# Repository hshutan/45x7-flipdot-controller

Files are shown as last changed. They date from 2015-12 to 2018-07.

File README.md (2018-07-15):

**This project is old! I do not recommend my hardware based project anymore, check out my RS-485 protocol-based projects! [Main Flipdot Project Page Here](https://github.com/hshutan/FlipDotCompendium)**

---

Flip Dot Animation 1

# 45x7-flipdot-controller
Custom PCB controller board for a single 45x7 flip dot panel from a Luminator MAX3000 SideSign

PCBFront PCBBack

Finished PCB Flip Dot Animation 2 

# How To

**A much more [detailed How To](#detailed) is below**

You will need the following items to assemble a flip dot sign using my PCB

1. The PCB in this github project which can be ordered from [OSH Park](https://oshpark.com/shared_projects/JROcn5LK) or another fab.
2. [My simple Arduino clock program](https://github.com/hshutan/FlipDotDisplay_Clock1_SWv1) which contains my `Matrix_CoProcessor` library, a library specifically built to drive this PCB.
3. Surface mount silicon parts: see the [Digi-Key BOM file](https://github.com/hshutan/45x7-flipdot-controller/blob/master/FlipDotBOM.csv)
  - Note that the Digi-Key BOM does not include the two through hole capacitors you will need.
4. A Luminator MAX3000 Side Sign.
  - I purchased mine from [Rollsign Gallery](http://rollsigngallery.com/). A single Luminator MAX3000 side sign will have two 45x7 display panels inside, which are very easy to remove.
5. A microcontroller or Arduino, and various power supply components to provide the different needed voltages.
  - I like Paul Stoffregen's Arduino compatible [Teensy](http://www.pjrc.com/) but often use [Arduino Pro Mini](https://www.arduino.cc/en/Main/ArduinoBoardProMini) clones from eBay for less demanding projects.

# Notes
The silkscreen for the 64 pin connector is for aesthetics. You should install the connector on the back of the board not the front, using the silkscreen for orientation reference only.

There are three voltages: Logic (5v), Flip (12-15v), LED (19v or 400mA max)

HW Rev1 of the PCB does not include any current limiting for the flip dots, or for the LEDs. I am using a 60mA current limiter in-line with the flip dot voltage line. The dots seem to flip best based on voltage and not current, which is why I am using such a small current. The LEDs are meant to be driven at 19 volts max, however less is safer. A current limit of 350mA would be safe for the LEDs.

My first prototype clock/sign with this PCB uses 15 volts for both the LEDs and flip dots. This means the LEDs are always on, although not near their maximum brightness. I am using a 5 volt Arduino Pro Mini, and also supplying 5 volts to the logic voltage input on the PCB.

Watch for ground loops, as I believe these cause weak/un-reliable flips. Because the grounds are all "commoned" on the PCB, do not tie any of your grounds together pre-PCB.

Luminator and MAX3000 are trade names of the Luminator Technology Group, not mine.

# Detailed How To / Step by Step Instructions
1. Acquire a Luminator MAX3000 Side Sign. I found mine on [Rollsign Gallery](http://rollsigngallery.com/).
  - A single Luminator side sign will contain two 45x7 panels.
2. Order the PCB in this github project, it can be ordered with a few clicks from [OSH Park](https://oshpark.com/shared_projects/JROcn5LK)
3. Order the bill of materials ([see CSV file](https://github.com/hshutan/45x7-flipdot-controller/blob/master/FlipDotBOM.csv))
  - Also grab two spare through hole capacitors from your parts bin. Try a 50 volt 330 microfarad for the flip voltage, and a 16 volt 100 microfarad capacitor for the logic voltage.
4. Take apart the MAX3000 side sign and remove both of the 45x7 panels.
5. Assemble the PCB by placing all components and soldering. Hot air can be used for all the surface mount components.
  - For aesthetics, the PCB has very little silk screen. Here is how to place components: Pin 1 of each IC is in the lower left of the land pattern when viewing the board from the top (see PCB pictures at the top of this page).
  - The 0805 (2012 Metric) pads in the lower right area of the PCB are for the pull-up and pull-down resistors.
  - The 0805 (2012 Metric) pads in the upper left of the PCB are for the 0.1 microfarad shift register supporting capacitors.
6. Program an Arduino or microcontroller with the [test pattern](https://github.com/hshutan/FlipDotDisplay_TestPatterns_SWv1) software. A good test pattern to start with is `testPattern2()`
7. Hook up the Arduino per the comments in the code:
  - Arduino Uno pin 11, to SER on PCB
  - Arduino Uno pin 13, to SCK on PCB
  - Arduino Uno pin 10, to RCK on PCB
  - Arduino 5v, to 5v+ on PCB
8. Connect a power supply (start with 10-12 volts) to GND and Flip+ on the PCB.
  - For prototyping, use a constant voltage/constant current power supply. This will allow you to limit the current to 100mA (or less) for safety, and also to test flip reliability at different voltages. If you are using my `Matrix_CoProcessor` library that comes with the [test pattern](https://github.com/hshutan/FlipDotDisplay_TestPatterns_SWv1) software, then there is little risk of a flip dot being energized for more than a few hundred microseconds, however you should still use current limiting of 100mA or less to prevent damage if any paths remain energized for too long.

# Thanks
I would like to thank the following sources:
- [Dottie the Flip Dot Clock](http://dhenshaw.com/Art/Dottie/start.html)
- [Rollsign Gallery](http://rollsigngallery.com/)

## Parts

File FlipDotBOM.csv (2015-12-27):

暼繢igi-Key Part Number | Manufacturer | Manufacturer Part Number | Customer Reference | Quantity 1 | Quantity 2 | Quantity 3 | Mfg Std Lead Time | Description | Comments | RoHS Status | Lead Free Status | REACH Status
5650458-5-ND | TE CONNECTIVITY AMP | 5650458-5 | AMPFEMALESOCK64OF96POS | 1 | 0 | 0 | 5 Weeks | CONN RECEPT 64 POS VERT DIN PCB |  | RoHS Compliant | Lead free | Not Available
490-1673-1-ND | MURATA ELECTRONICS (VA) | GRM21BR71E104KA01L | CAPFORSHIFTREGS | 13 | 0 | 0 | 18 Weeks | CAP CER 0.1UF 25V X7R 0805 | Alternate Packaging Exists | RoHS Compliant | Lead free | Unaffected Jun-2015
IRF7309PBFCT-ND | INFINEON TECHNOLOGIES AMERICAS CORP. (VA) | IRF7309TRPBF | NONCOMMONDRAINOEMPNFET | 52 | 0 | 0 | 12 Weeks | MOSFET N/P-CH 30V 4A/3A 8SOIC | Alternate Packaging Exists | RoHS Compliant | Lead free | Unaffected Jun-2015
296-26485-1-ND | TEXAS INSTRUMENTS (VA) | SN74HC595NSR | TILATCHINGSHIFTREGR | 13 | 0 | 0 | 6 Weeks | IC SHIFT REGISTER 8BIT 16SO | Alternate Packaging Exists | RoHS Compliant | Lead free | Unaffected Dec-2014
NSI45060JDT4GOSCT-ND | ON SEMICONDUCTOR (VA) | NSI45060JDT4G | CURLIMTR | 1 | 0 | 0 | 13 Weeks | IC LED DRVR SBT CCR DPAK | Alternate Packaging Exists | RoHS Compliant | Lead free | Unaffected Jun-2015
YAG1319CT-ND | YAGEO (VA) | RC0805FR-0710KP | 10K1%2012 | 14 | 0 | 0 | 22 Weeks | RES SMD 10K OHM 1% 1/8W 0805 | Alternate Packaging Exists | RoHS Compliant | Lead free | Unaffected Jun-2015

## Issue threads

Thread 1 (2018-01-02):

Problem switching off high side P channel MOSFETs

iiliev, 2018-01-02:
Thank you so much for posting your project! I did get one of these MAX3000 flip dot displays with no driver and your schematic is the closest to what I need (mine is 16x28 though). The principle of operation is clear, the code works fine, I can't figure out how are you switching off the high side P channel MOSFETs though. The P channel MOSFET in IRF7309TRPBF has a switching voltage of -1V. When you power the load (the flip dot display in this case) with say 12V and the switching voltage (from Arduino/microcontroller/SN74HC595/etc) is 5V the gate sees -7V. On the Eagle schematic you posted it seems that all MOSFETs are driven directly by the SN74HC595. Am I missing something (the only way I know how to do this would be with at least one extra transistor)? Appreciate your help...

hshutan, 2018-01-03:
Hi! Happy to share the project. Hopefully I can help. I will say that it is _very_ possible that I am not using components (like PNP/NPN transistors) _entirely_ correctly...but the clock I built is still running 24/7 perfectly!

The way I am using these MOSFETs from my hobby-level understanding, is that a logic HIGH (5v) from a shift register going to an NPN's gate or base would turn that NPN 'switch' on. A logic HIGH (5v) from a shift register going to a PNP's gate or base would turn that PNP 'switch' off. Same thing in reverse, logic LOW (0v) would turn an NPN off and a PNP on. That's why the idle or steady state of the shift registers is a stream of alternating 1's and 0's, it sets all the PNPs turned off with logic HIGHs, and all the NPNs turned off with logic LOWs.

I don't think I understand what you mean about the negative voltage unless it is related to my own mis-understanding of the way PNP transistors work, but I can say you don't need to supply any negative voltages with my design. The way I get dots to flip on and off is by just running the current (12 volt line in your case) through the dot forwards or backwards depending on which column NPN/PNP and which row NPN/PNP switches the code opens up. Your sign could possibly be electrically different than mine, but I think that is unlikely. Have you probed out the connector of your sign to identify the row pins and column pins? I found on mine that the row pins had individual pins for forwards and backwards current, so for my 7 row sign, there were 14 pins, two per row. But each column only had 1 pin that is used for both forwards and reverse current.

This method I am using may not be the most correct, and certainly isn't the best way to drive the dots, at least in terms of display update performance, but it should be working. Have you isolated your test hardware down to a single flip dot? I started with a single x,y position, once I got that turning on and off reliably (experiment with different pulse lengths and number of pulses), I moved to controlling two dots in a single column, then a whole column, then two columns. Once I confirmed two columns and the ability to individually address dots, I expanded my design to the one I'm using now.

By the way, that schematic was literally the first schematic and first PCB I ever designed, so I apologize for the mess of nets in the drawing, I didn't think before I drew it!

Curious to hear if that helps at all...

iiliev, 2018-01-03:
Thanks for the quick reply! The first response here summarizes the problem - https://forum.arduino.cc/index.php?topic=377056.0 The correct way of doing it is like so - https://wiki.attraktor.org/File:Flipdotpixel.png. See the extra NPN transistors on the P channel MOSFETs), your schematic (and board pictures) do not include those. I assume you might have been lucky and it's possible this worked, but wanted to make sure I am not missing something. Anyways, thanks again for your help!

hshutan, 2018-01-03:
That flipdot diagram is interesting, new to me! I am positive there is some luck involved, and this design difference could explain why I never could get faster update, or stronger flip performance out of my sign -- my design is probably running right on some electrical thresholds. Good luck, if you come up with something good please share it!

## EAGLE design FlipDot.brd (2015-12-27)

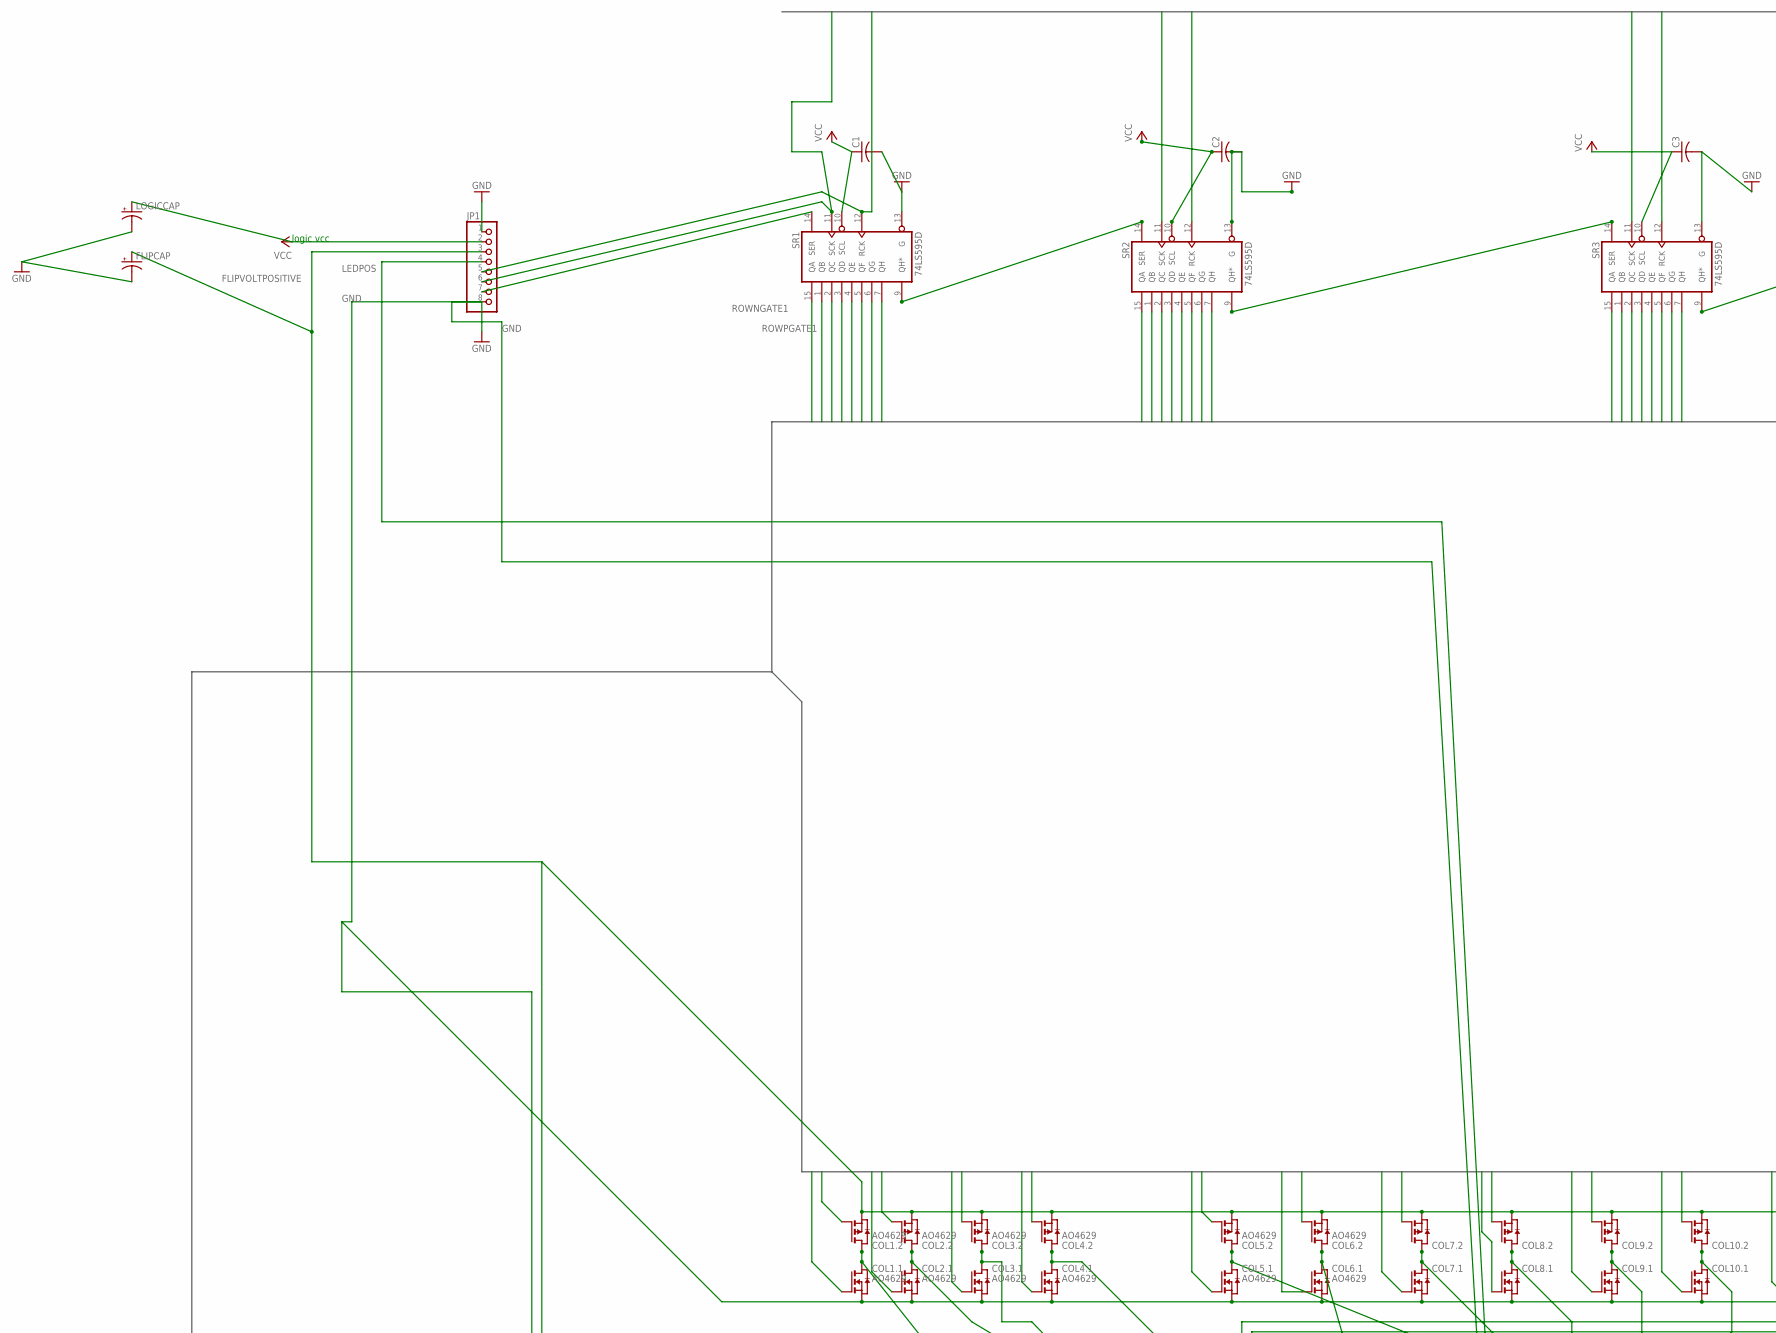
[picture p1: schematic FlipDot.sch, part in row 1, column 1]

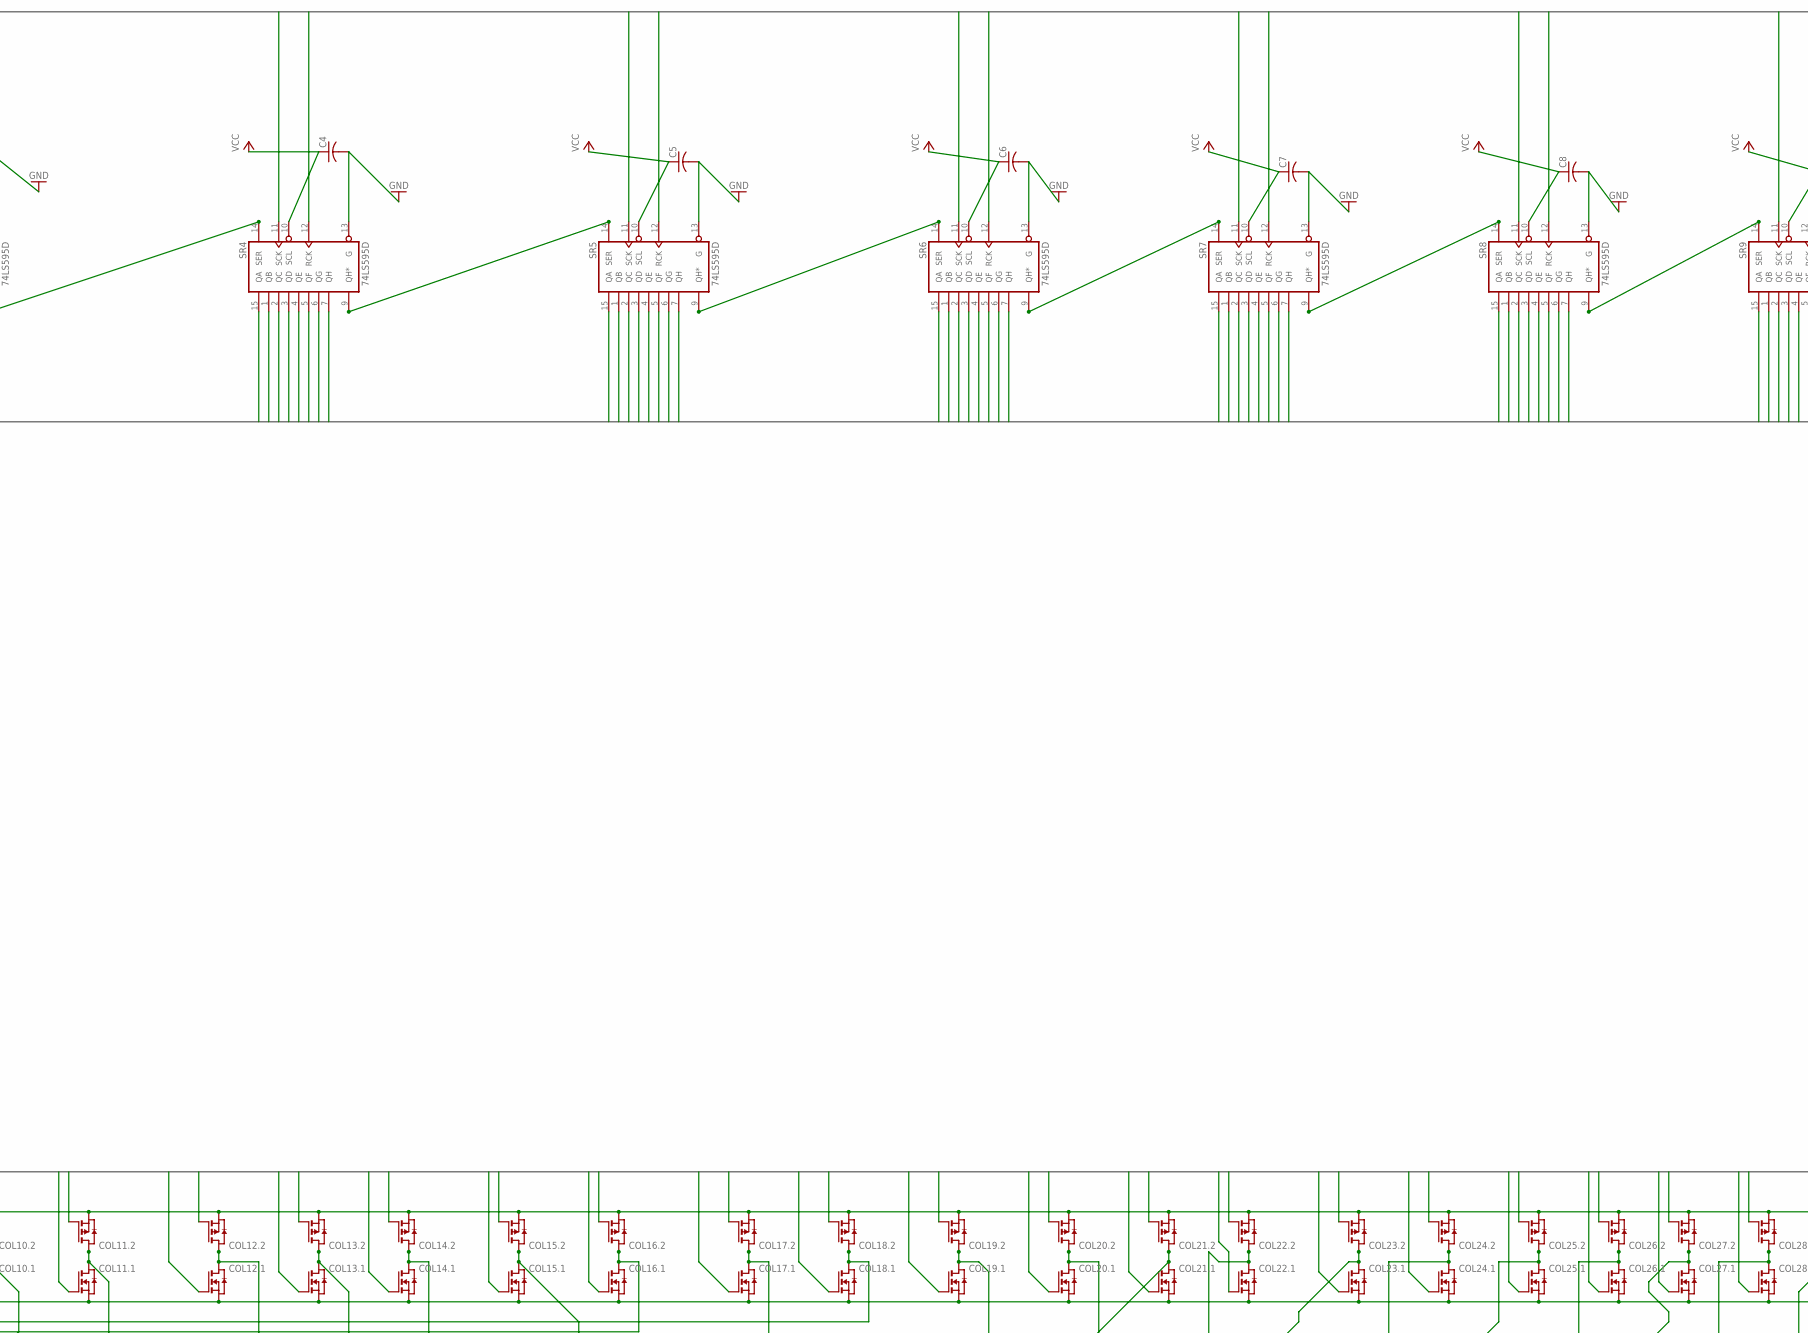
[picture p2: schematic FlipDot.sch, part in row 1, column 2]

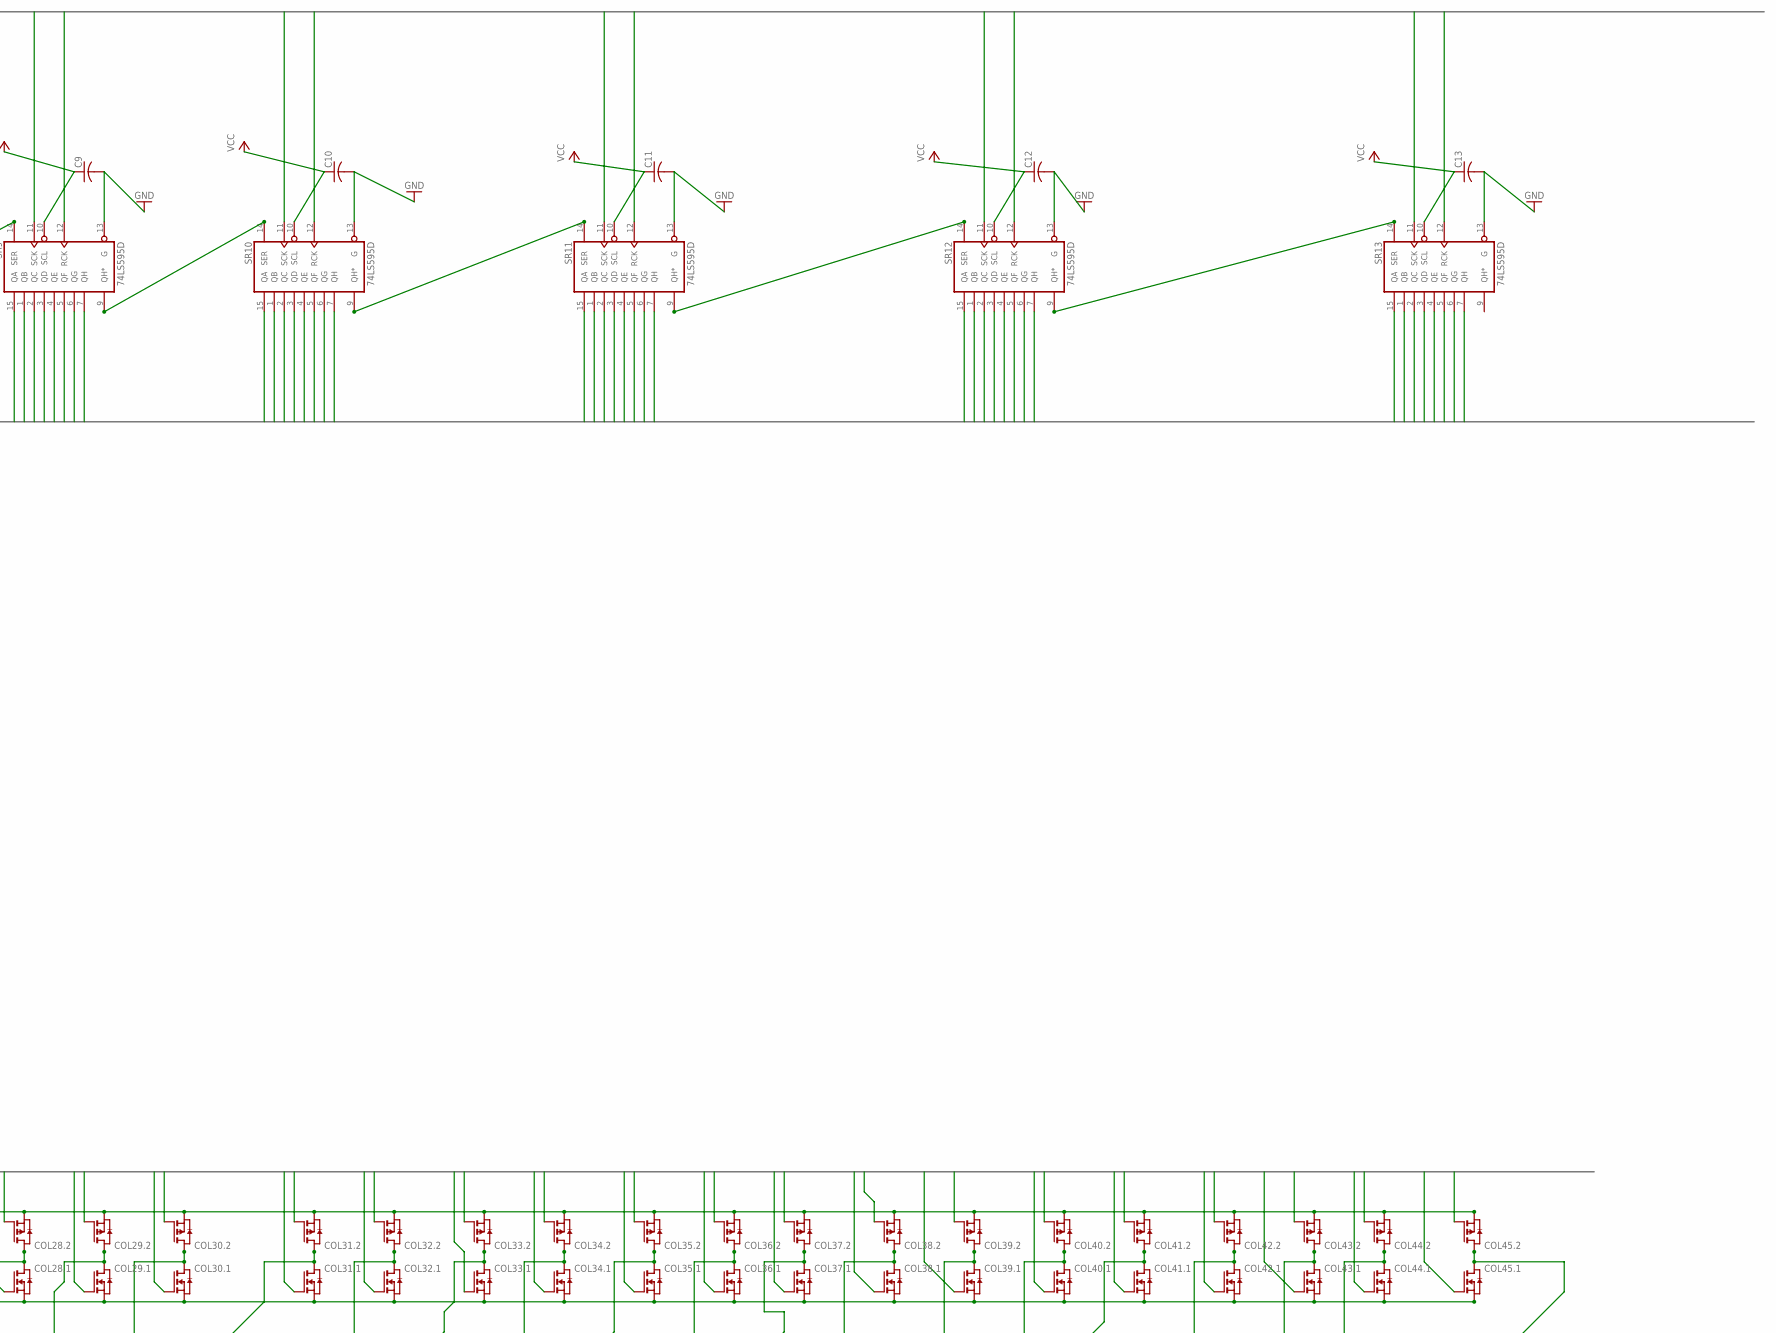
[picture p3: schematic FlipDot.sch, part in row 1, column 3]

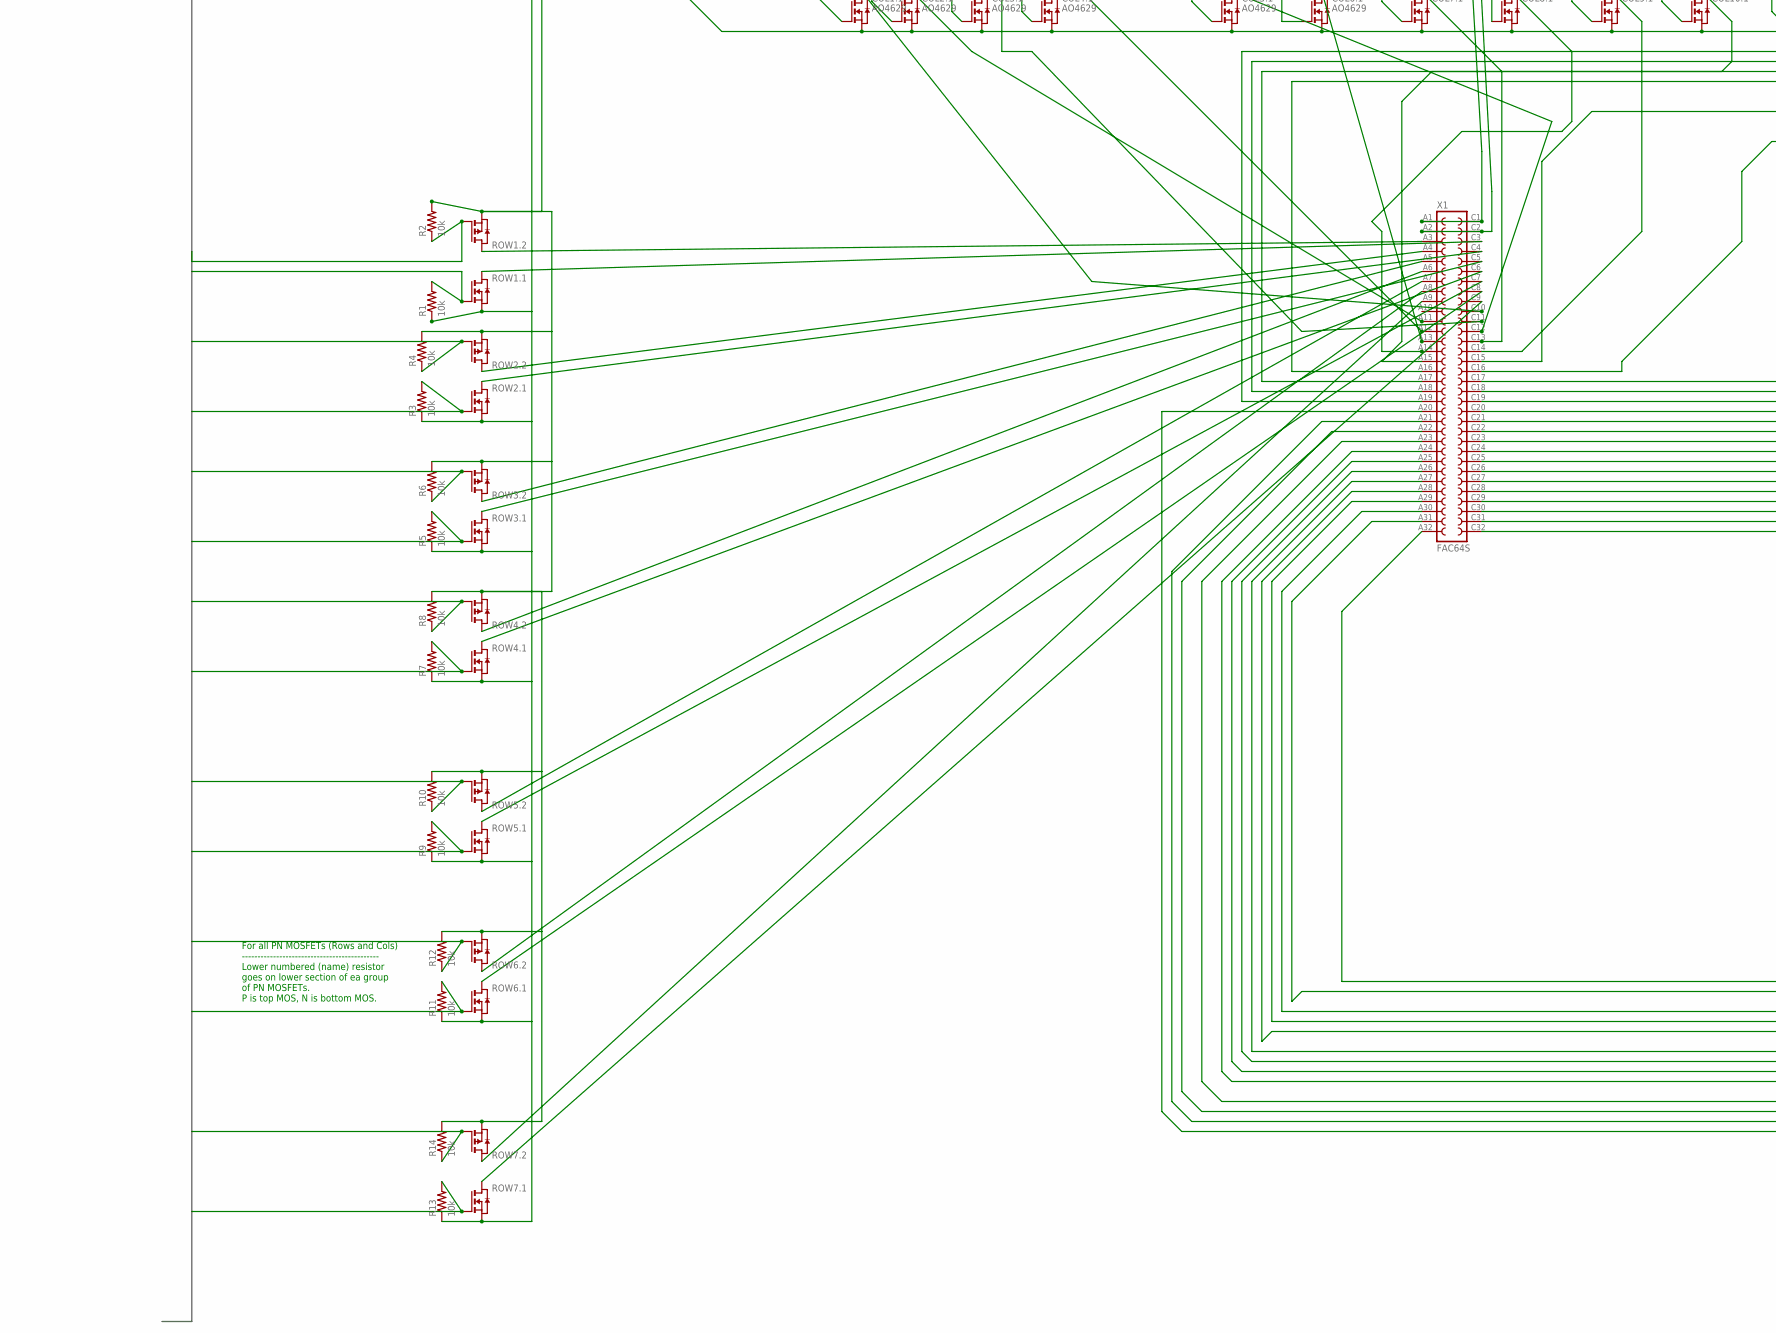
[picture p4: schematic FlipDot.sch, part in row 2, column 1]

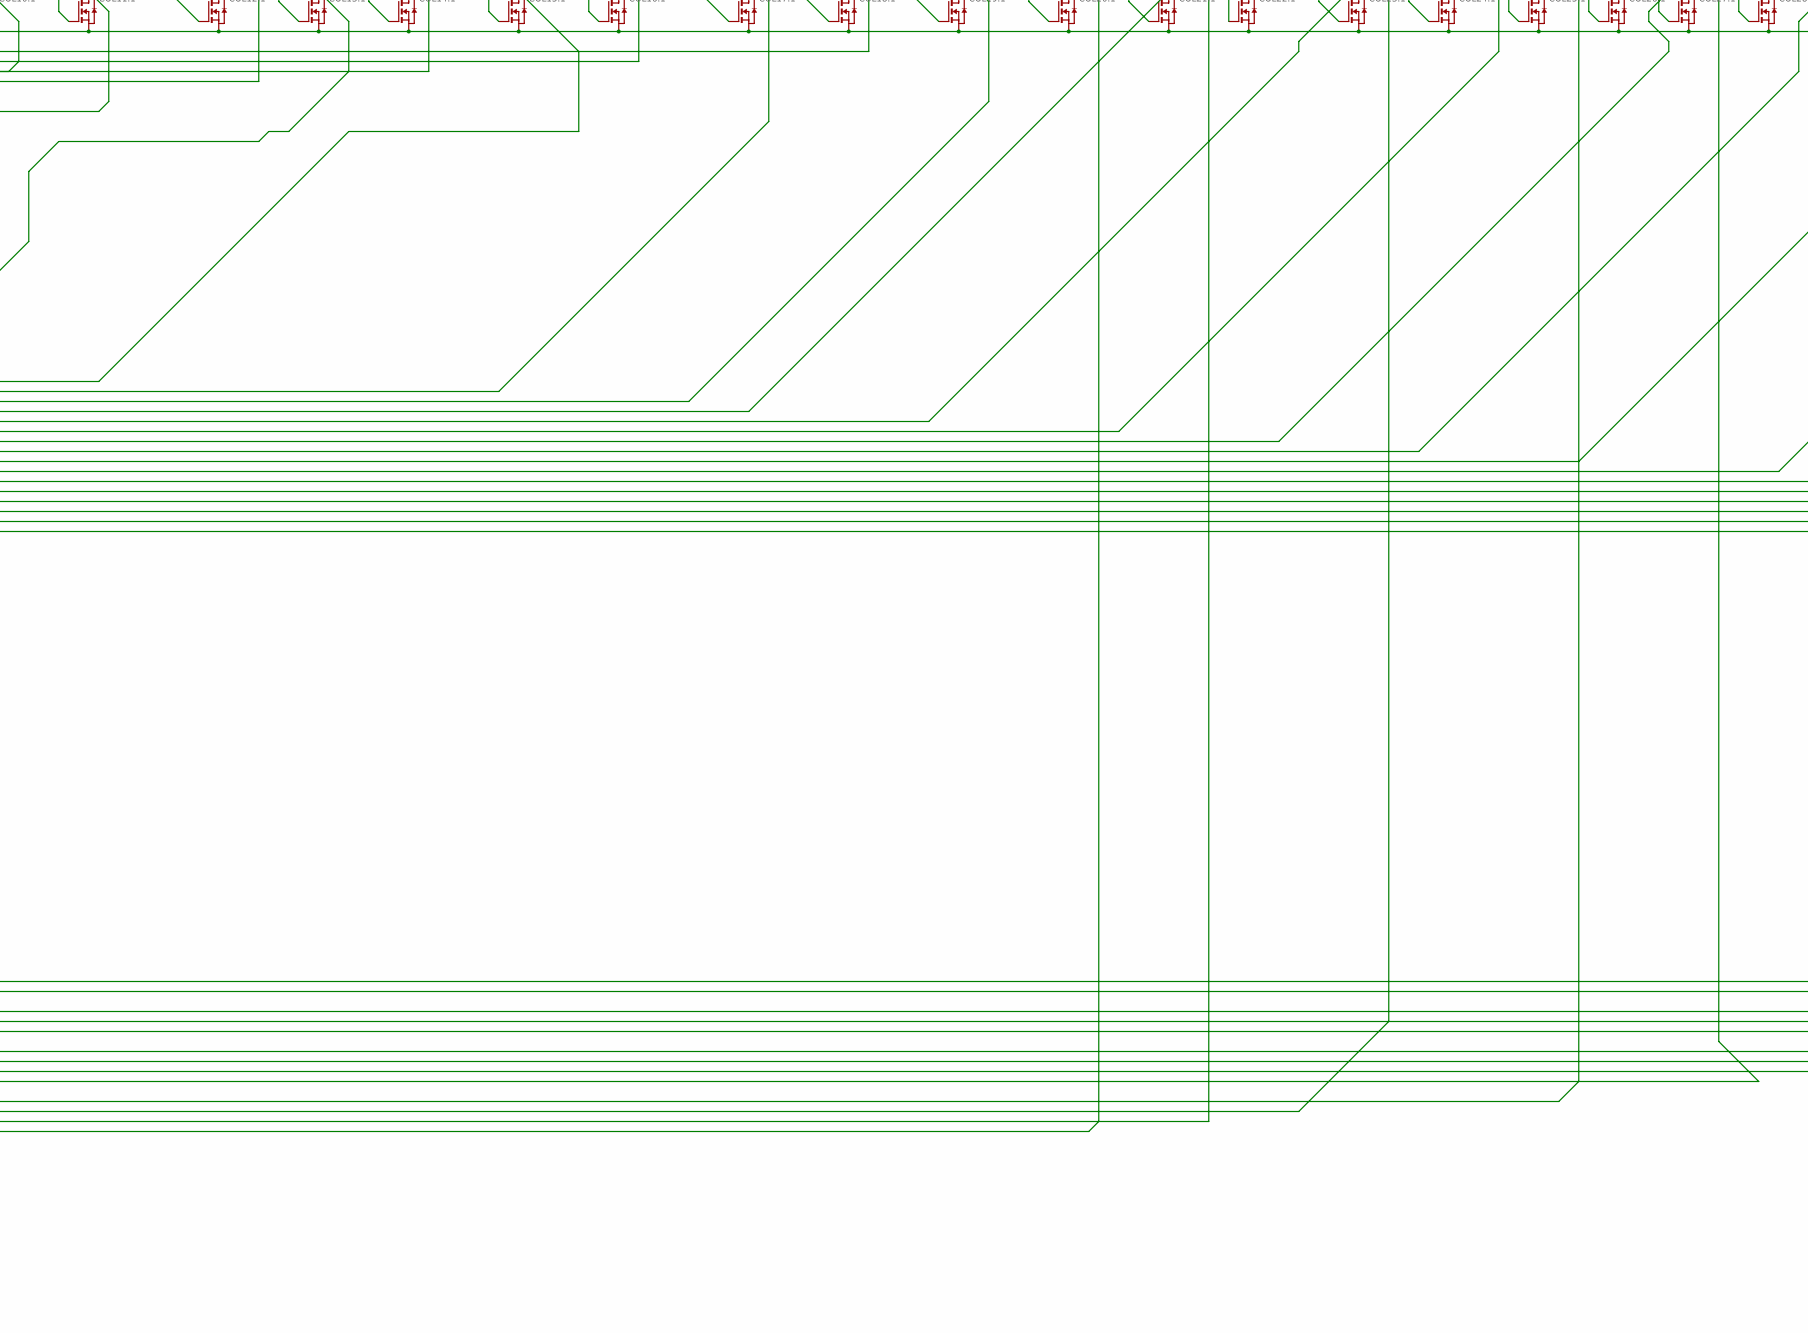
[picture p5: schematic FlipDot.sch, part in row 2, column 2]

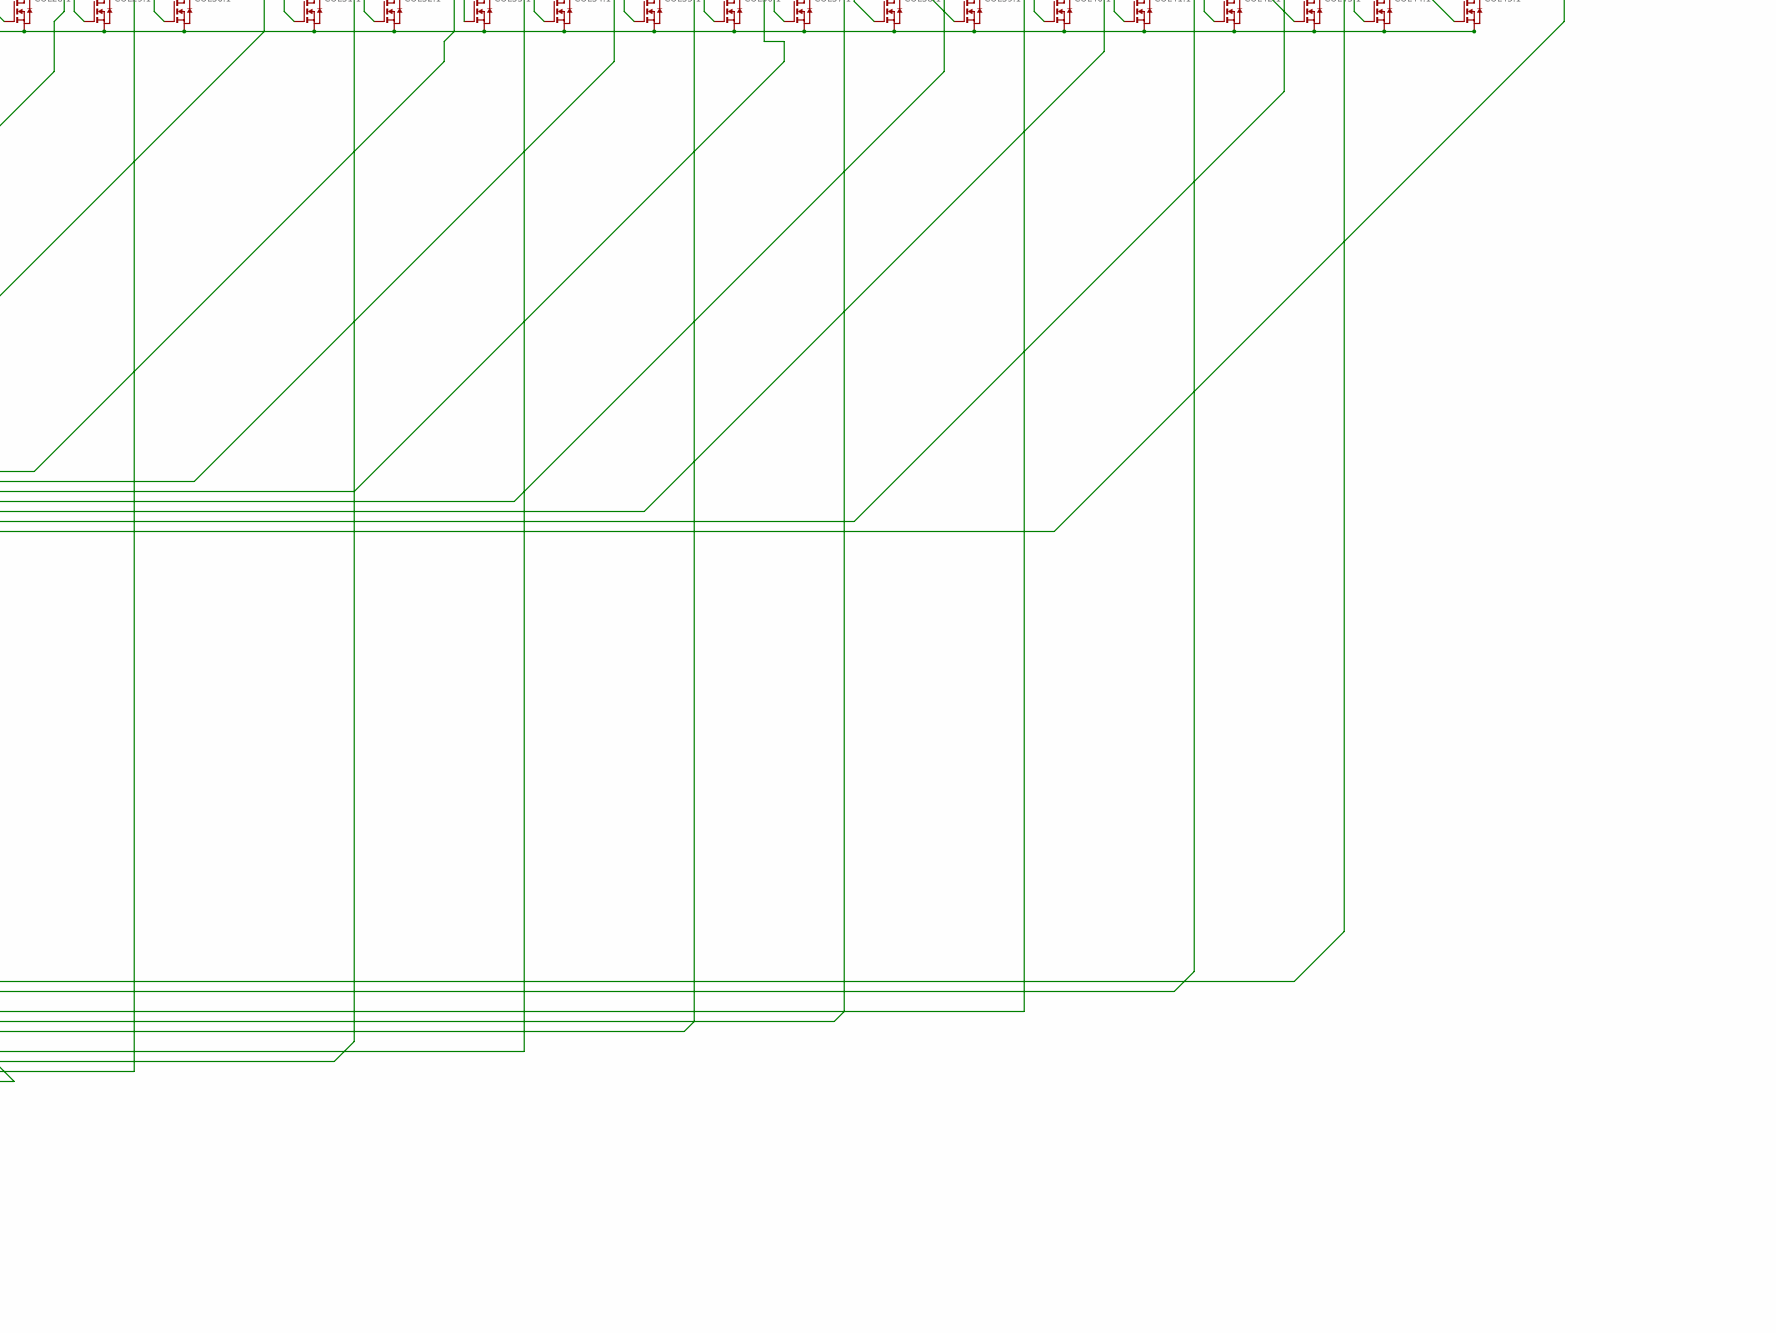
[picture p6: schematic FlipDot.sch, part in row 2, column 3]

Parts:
C1, C2, C3, C4, C5, C6, C7, C8, C9, C10, C11, C12, C13: C-USC2012; C2012
COL1., COL2., COL3., COL4., COL5., COL6.: AO4629; SO8
COL7., COL8., COL9., COL10., COL11., COL12., COL13., COL14., COL15., COL16., COL17., COL18., COL19., COL20., COL21., COL22., COL23., COL24., COL25., COL26., COL27., COL28., COL29., COL30., COL31., COL32., COL33., COL34., COL35., COL36., COL37., COL38., COL39., COL40., COL41., COL42., COL43., COL44., COL45.: PN_MOSFET-SO8; SO8
FLIPCAP: CPOL-USE5-10.5; E5-10,5
JP1: PINHD-1X8; 1X08
LOGICCAP: CPOL-USE5-10.5; E5-10,5
R1, R2, R3, R4, R5, R6, R7, R8, R9, R10, R11, R12, R13, R14: 10k; R2012
ROW1., ROW2., ROW3., ROW4., ROW5., ROW6., ROW7.: PN_MOSFET-SO8; SO8
SR1, SR2, SR3, SR4, SR5, SR6, SR7, SR8, SR9, SR10, SR11, SR12, SR13: 74LS595D; SO16
X1: FAC64S

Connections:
COL1COMMON: COL1..5 (D), COL1..6 (D), COL1..7 (D), COL1..8 (D), X1.C10
COL2COMMON: COL2..5 (D), COL2..6 (D), COL2..7 (D), COL2..8 (D), X1.A11
COL3COMMON: COL3..5 (D), COL3..6 (D), COL3..7 (D), COL3..8 (D), X1.C11
COL4COMMON: COL4..5 (D), COL4..6 (D), COL4..7 (D), COL4..8 (D), X1.A12
COL5COMMON: COL5..5 (D), COL5..6 (D), COL5..7 (D), COL5..8 (D), X1.C12
COL6COMMON: COL6..5 (D), COL6..6 (D), COL6..7 (D), COL6..8 (D), X1.A13
COL7COMMON: COL7..5 (D), COL7..6 (D), COL7..7 (D), COL7..8 (D), X1.C13
COL8COMMON: COL8..5 (D), COL8..6 (D), COL8..7 (D), COL8..8 (D), X1.A14
COL9COMMON: COL9..5 (D), COL9..6 (D), COL9..7 (D), COL9..8 (D), X1.C14
COL10COMMON: COL10..5 (D), COL10..6 (D), COL10..7 (D), COL10..8 (D), X1.A15
COL11COMMON: COL11..5 (D), COL11..6 (D), COL11..7 (D), COL11..8 (D), X1.C15
COL12COMMON: COL12..5 (D), COL12..6 (D), COL12..7 (D), COL12..8 (D), X1.A16
COL13COMMON: COL13..5 (D), COL13..6 (D), COL13..7 (D), COL13..8 (D), X1.C16
COL14COMMON: COL14..5 (D), COL14..6 (D), COL14..7 (D), COL14..8 (D), X1.A17
COL15COMMON: COL15..5 (D), COL15..6 (D), COL15..7 (D), COL15..8 (D), X1.C17
COL16COMMON: COL16..5 (D), COL16..6 (D), COL16..7 (D), COL16..8 (D), X1.A18
COL17COMMON: COL17..5 (D), COL17..6 (D), COL17..7 (D), COL17..8 (D), X1.C18
COL18COMMON: COL18..5 (D), COL18..6 (D), COL18..7 (D), COL18..8 (D), X1.A19
COL19COMMON: COL19..5 (D), COL19..6 (D), COL19..7 (D), COL19..8 (D), X1.C19
COL20COMMON: COL20..5 (D), COL20..6 (D), COL20..7 (D), COL20..8 (D), X1.A20
COL21COMMON: COL21..5 (D), COL21..6 (D), COL21..7 (D), COL21..8 (D), X1.C20
COL22COMMON: COL22..5 (D), COL22..6 (D), COL22..7 (D), COL22..8 (D), X1.A21
COL23COMMON: COL23..5 (D), COL23..6 (D), COL23..7 (D), COL23..8 (D), X1.C21
COL24COMMON: COL24..5 (D), COL24..6 (D), COL24..7 (D), COL24..8 (D), X1.A22
COL25COMMON: COL25..5 (D), COL25..6 (D), COL25..7 (D), COL25..8 (D), X1.C22
COL26COMMON: COL26..5 (D), COL26..6 (D), COL26..7 (D), COL26..8 (D), X1.A23
COL27COMMON: COL27..5 (D), COL27..6 (D), COL27..7 (D), COL27..8 (D), X1.C23
COL28COMMON: COL28..5 (D), COL28..6 (D), COL28..7 (D), COL28..8 (D), X1.A24
COL29COMMON: COL29..5 (D), COL29..6 (D), COL29..7 (D), COL29..8 (D), X1.C24
COL30COMMON: COL30..5 (D), COL30..6 (D), COL30..7 (D), COL30..8 (D), X1.A25
COL31COMMON: COL31..5 (D), COL31..6 (D), COL31..7 (D), COL31..8 (D), X1.C25
COL32COMMON: COL32..5 (D), COL32..6 (D), COL32..7 (D), COL32..8 (D), X1.A26
COL33COMMON: COL33..5 (D), COL33..6 (D), COL33..7 (D), COL33..8 (D), X1.C26
COL34COMMON: COL34..5 (D), COL34..6 (D), COL34..7 (D), COL34..8 (D), X1.A27
COL35COMMON: COL35..5 (D), COL35..6 (D), COL35..7 (D), COL35..8 (D), X1.C27
COL36COMMON: COL36..5 (D), COL36..6 (D), COL36..7 (D), COL36..8 (D), X1.A28
COL37COMMON: COL37..5 (D), COL37..6 (D), COL37..7 (D), COL37..8 (D), X1.C28
COL38COMMON: COL38..5 (D), COL38..6 (D), COL38..7 (D), COL38..8 (D), X1.A29
COL39COMMON: COL39..5 (D), COL39..6 (D), COL39..7 (D), COL39..8 (D), X1.C29
COL40COMMON: COL40..5 (D), COL40..6 (D), COL40..7 (D), COL40..8 (D), X1.A30
COL41COMMON: COL41..5 (D), COL41..6 (D), COL41..7 (D), COL41..8 (D), X1.C30
COL42COMMON: COL42..5 (D), COL42..6 (D), COL42..7 (D), COL42..8 (D), X1.A31
COL43COMMON: COL43..5 (D), COL43..6 (D), COL43..7 (D), COL43..8 (D), X1.C31
COL44COMMON: COL44..5 (D), COL44..6 (D), COL44..7 (D), COL44..8 (D), X1.A32
COL45COMMON: COL45..5 (D), COL45..6 (D), COL45..7 (D), COL45..8 (D), X1.C32
COLNGATE1: COL1..2 (G), SR2.6 (QG)
COLNGATE2: COL2..2 (G), SR3.15 (QA)
COLNGATE3: COL3..2 (G), SR3.2 (QC)
COLNGATE4: COL4..2 (G), SR3.4 (QE)
COLNGATE5: COL5..2 (G), SR3.6 (QG)
COLNGATE6: COL6..2 (G), SR4.15 (QA)
COLNGATE7: COL7..2 (G), SR4.2 (QC)
COLNGATE8: COL8..2 (G), SR4.4 (QE)
COLNGATE9: COL9..2 (G), SR4.6 (QG)
COLNGATE10: COL10..2 (G), SR5.15 (QA)
COLNGATE11: COL11..2 (G), SR5.2 (QC)
COLNGATE12: COL12..2 (G), SR5.4 (QE)
COLNGATE13: COL13..2 (G), SR5.6 (QG)
COLNGATE14: COL14..2 (G), SR6.15 (QA)
COLNGATE15: COL15..2 (G), SR6.2 (QC)
COLNGATE16: COL16..2 (G), SR6.4 (QE)
COLNGATE17: COL17..2 (G), SR6.6 (QG)
COLNGATE18: COL18..2 (G), SR7.15 (QA)
COLNGATE19: COL19..2 (G), SR7.2 (QC)
COLNGATE20: COL20..2 (G), SR7.4 (QE)
COLNGATE21: COL21..2 (G), SR7.6 (QG)
COLNGATE22: COL22..2 (G), SR8.15 (QA)
COLNGATE23: COL23..2 (G), SR8.2 (QC)
COLNGATE24: COL24..2 (G), SR8.4 (QE)
COLNGATE25: COL25..2 (G), SR8.6 (QG)
COLNGATE26: COL26..2 (G), SR9.15 (QA)
COLNGATE27: COL27..2 (G), SR9.2 (QC)
COLNGATE28: COL28..2 (G), SR9.4 (QE)
COLNGATE29: COL29..2 (G), SR9.6 (QG)
COLNGATE30: COL30..2 (G), SR10.15 (QA)
COLNGATE31: COL31..2 (G), SR10.2 (QC)
COLNGATE32: COL32..2 (G), SR10.4 (QE)
COLNGATE33: COL33..2 (G), SR10.6 (QG)
COLNGATE34: COL34..2 (G), SR11.15 (QA)
COLNGATE35: COL35..2 (G), SR11.2 (QC)
COLNGATE36: COL36..2 (G), SR11.4 (QE)
COLNGATE37: COL37..2 (G), SR11.6 (QG)
COLNGATE38: COL38..2 (G), SR12.15 (QA)
COLNGATE39: COL39..2 (G), SR12.2 (QC)
COLNGATE40: COL40..2 (G), SR12.4 (QE)
COLNGATE41: COL41..2 (G), SR12.6 (QG)
COLNGATE42: COL42..2 (G), SR13.15 (QA)
COLNGATE43: COL43..2 (G), SR13.2 (QC)
COLNGATE44: COL44..2 (G), SR13.4 (QE)
COLNGATE45: COL45..2 (G), SR13.6 (QG)
COLPGATE1: COL1..4 (G), SR2.7 (QH)
COLPGATE2: COL2..4 (G), SR3.1 (QB)
COLPGATE3: COL3..4 (G), SR3.3 (QD)
COLPGATE4: COL4..4 (G), SR3.5 (QF)
COLPGATE5: COL5..4 (G), SR3.7 (QH)
COLPGATE6: COL6..4 (G), SR4.1 (QB)
COLPGATE7: COL7..4 (G), SR4.3 (QD)
COLPGATE8: COL8..4 (G), SR4.5 (QF)
COLPGATE9: COL9..4 (G), SR4.7 (QH)
COLPGATE10: COL10..4 (G), SR5.1 (QB)
COLPGATE11: COL11..4 (G), SR5.3 (QD)
COLPGATE12: COL12..4 (G), SR5.5 (QF)
COLPGATE13: COL13..4 (G), SR5.7 (QH)
COLPGATE14: COL14..4 (G), SR6.1 (QB)
COLPGATE15: COL15..4 (G), SR6.3 (QD)
COLPGATE16: COL16..4 (G), SR6.5 (QF)
COLPGATE17: COL17..4 (G), SR6.7 (QH)
COLPGATE18: COL18..4 (G), SR7.1 (QB)
COLPGATE19: COL19..4 (G), SR7.3 (QD)
COLPGATE20: COL20..4 (G), SR7.5 (QF)
COLPGATE21: COL21..4 (G), SR7.7 (QH)
COLPGATE22: COL22..4 (G), SR8.1 (QB)
COLPGATE23: COL23..4 (G), SR8.3 (QD)
COLPGATE24: COL24..4 (G), SR8.5 (QF)
COLPGATE25: COL25..4 (G), SR8.7 (QH)
COLPGATE26: COL26..4 (G), SR9.1 (QB)
COLPGATE27: COL27..4 (G), SR9.3 (QD)
COLPGATE28: COL28..4 (G), SR9.5 (QF)
COLPGATE29: COL29..4 (G), SR9.7 (QH)
COLPGATE30: COL30..4 (G), SR10.1 (QB)
COLPGATE31: COL31..4 (G), SR10.3 (QD)
COLPGATE32: COL32..4 (G), SR10.5 (QF)
COLPGATE33: COL33..4 (G), SR10.7 (QH)
COLPGATE34: COL34..4 (G), SR11.1 (QB)
COLPGATE35: COL35..4 (G), SR11.3 (QD)
COLPGATE36: COL36..4 (G), SR11.5 (QF)
COLPGATE37: COL37..4 (G), SR11.7 (QH)
COLPGATE38: COL38..4 (G), SR12.1 (QB)
COLPGATE39: COL39..4 (G), SR12.3 (QD)
COLPGATE40: COL40..4 (G), SR12.5 (QF)
COLPGATE41: COL41..4 (G), SR12.7 (QH)
COLPGATE42: COL42..4 (G), SR13.1 (QB)
COLPGATE43: COL43..4 (G), SR13.3 (QD)
COLPGATE44: COL44..4 (G), SR13.5 (QF)
COLPGATE45: COL45..4 (G), SR13.7 (QH)
FLIPVOLTPOSITIVE: COL1..3 (S), COL2..3 (S), COL3..3 (S), COL4..3 (S), COL5..3 (S), COL6..3 (S), COL7..3 (S), COL8..3 (S), COL9..3 (S), COL10..3 (S), COL11..3 (S), COL12..3 (S), COL13..3 (S), COL14..3 (S), COL15..3 (S), COL16..3 (S), COL17..3 (S), COL18..3 (S), COL19..3 (S), COL20..3 (S), COL21..3 (S), COL22..3 (S), COL23..3 (S), COL24..3 (S), COL25..3 (S), COL26..3 (S), COL27..3 (S), COL28..3 (S), COL29..3 (S), COL30..3 (S), COL31..3 (S), COL32..3 (S), COL33..3 (S), COL34..3 (S), COL35..3 (S), COL36..3 (S), COL37..3 (S), COL38..3 (S), COL39..3 (S), COL40..3 (S), COL41..3 (S), COL42..3 (S), COL43..3 (S), COL44..3 (S), COL45..3 (S), FLIPCAP.+, JP1.3, R2.2, R4.2, R6.2, R8.2, R10.2, R12.2, R14.2, ROW1..3 (S), ROW2..3 (S), ROW3..3 (S), ROW4..3 (S), ROW5..3 (S), ROW6..3 (S), ROW7..3 (S)
GND: C1.2, C2.2, C3.2, C4.2, C5.2, C6.2, C7.2, C8.2, C9.2, C10.2, C11.2, C12.2, C13.2, COL1..1 (S), COL2..1 (S), COL3..1 (S), COL4..1 (S), COL5..1 (S), COL6..1 (S), COL7..1 (S), COL8..1 (S), COL9..1 (S), COL10..1 (S), COL11..1 (S), COL12..1 (S), COL13..1 (S), COL14..1 (S), COL15..1 (S), COL16..1 (S), COL17..1 (S), COL18..1 (S), COL19..1 (S), COL20..1 (S), COL21..1 (S), COL22..1 (S), COL23..1 (S), COL24..1 (S), COL25..1 (S), COL26..1 (S), COL27..1 (S), COL28..1 (S), COL29..1 (S), COL30..1 (S), COL31..1 (S), COL32..1 (S), COL33..1 (S), COL34..1 (S), COL35..1 (S), COL36..1 (S), COL37..1 (S), COL38..1 (S), COL39..1 (S), COL40..1 (S), COL41..1 (S), COL42..1 (S), COL43..1 (S), COL44..1 (S), COL45..1 (S), FLIPCAP.-, JP1.1, JP1.8, LOGICCAP.-, R1.1, R3.1, R5.1, R7.1, R9.1, R11.1, R13.1, ROW1..1 (S), ROW2..1 (S), ROW3..1 (S), ROW4..1 (S), ROW5..1 (S), ROW6..1 (S), ROW7..1 (S), SR1.8 (GND), SR1.13 (G), SR2.8 (GND), SR2.13 (G), SR3.8 (GND), SR3.13 (G), SR4.8 (GND), SR4.13 (G), SR5.8 (GND), SR5.13 (G), SR6.8 (GND), SR6.13 (G), SR7.8 (GND), SR7.13 (G), SR8.8 (GND), SR8.13 (G), SR9.8 (GND), SR9.13 (G), SR10.8 (GND), SR10.13 (G), SR11.8 (GND), SR11.13 (G), SR12.8 (GND), SR12.13 (G), SR13.8 (GND), SR13.13 (G), X1.A1, X1.C1
LEDPOS: JP1.4, X1.A2, X1.C2
MAINSERIALLINE: JP1.7, SR1.14 (SER)
RCK: JP1.5, SR1.12 (RCK), SR2.12 (RCK), SR3.12 (RCK), SR4.12 (RCK), SR5.12 (RCK), SR6.12 (RCK), SR7.12 (RCK), SR8.12 (RCK), SR9.12 (RCK), SR10.12 (RCK), SR11.12 (RCK), SR12.12 (RCK), SR13.12 (RCK)
ROW1NCOM: ROW1..7 (D), ROW1..8 (D), X1.C3
ROW1PCOM: ROW1..5 (D), ROW1..6 (D), X1.A3
ROW2NCOM: ROW2..7 (D), ROW2..8 (D), X1.C4
ROW2PCOM: ROW2..5 (D), ROW2..6 (D), X1.A4
ROW3NCOM: ROW3..7 (D), ROW3..8 (D), X1.C5
ROW3PCOM: ROW3..5 (D), ROW3..6 (D), X1.A5
ROW4NCOM: ROW4..7 (D), ROW4..8 (D), X1.C6
ROW4PCOM: ROW4..5 (D), ROW4..6 (D), X1.A6
ROW5NCOM: ROW5..7 (D), ROW5..8 (D), X1.C7
ROW5PCOM: ROW5..5 (D), ROW5..6 (D), X1.A7
ROW6NCOM: ROW6..7 (D), ROW6..8 (D), X1.C8
ROW6PCOM: ROW6..5 (D), ROW6..6 (D), X1.A8
ROW7NCOM: ROW7..7 (D), ROW7..8 (D), X1.C9
ROW7PCOM: ROW7..5 (D), ROW7..6 (D), X1.A9
ROWNGATE1: R1.2, ROW1..2 (G), SR1.15 (QA)
ROWNGATE2: R3.2, ROW2..2 (G), SR1.2 (QC)
ROWNGATE3: R5.2, ROW3..2 (G), SR1.4 (QE)
ROWNGATE4: R7.2, ROW4..2 (G), SR1.6 (QG)
ROWNGATE5: R9.2, ROW5..2 (G), SR2.15 (QA)
ROWNGATE6: R11.2, ROW6..2 (G), SR2.2 (QC)
ROWNGATE7: R13.2, ROW7..2 (G), SR2.4 (QE)
ROWPGATE1: R2.1, ROW1..4 (G), SR1.1 (QB)
ROWPGATE2: R4.1, ROW2..4 (G), SR1.3 (QD)
ROWPGATE3: R6.1, ROW3..4 (G), SR1.5 (QF)
ROWPGATE4: R8.1, ROW4..4 (G), SR1.7 (QH)
ROWPGATE5: R10.1, ROW5..4 (G), SR2.1 (QB)
ROWPGATE6: R12.1, ROW6..4 (G), SR2.3 (QD)
ROWPGATE7: R14.1, ROW7..4 (G), SR2.5 (QF)
SCK: JP1.6, SR1.11 (SCK), SR2.11 (SCK), SR3.11 (SCK), SR4.11 (SCK), SR5.11 (SCK), SR6.11 (SCK), SR7.11 (SCK), SR8.11 (SCK), SR9.11 (SCK), SR10.11 (SCK), SR11.11 (SCK), SR12.11 (SCK), SR13.11 (SCK)
SR1TOSR2: SR1.9 (QH*), SR2.14 (SER)
SR2TOSR3: SR2.9 (QH*), SR3.14 (SER)
SR3TOSR4: SR3.9 (QH*), SR4.14 (SER)
SR4TOSR5: SR4.9 (QH*), SR5.14 (SER)
SR5TOSR6: SR5.9 (QH*), SR6.14 (SER)
SR6TOSR7: SR6.9 (QH*), SR7.14 (SER)
SR7TOSR8: SR7.9 (QH*), SR8.14 (SER)
SR8TOSR9: SR8.9 (QH*), SR9.14 (SER)
SR9TOSR10: SR9.9 (QH*), SR10.14 (SER)
SR10TOSR11: SR10.9 (QH*), SR11.14 (SER)
SR11TOSR12: SR11.9 (QH*), SR12.14 (SER)
SR12TOSR13: SR12.9 (QH*), SR13.14 (SER)
VCC: C1.1, C2.1, C3.1, C4.1, C5.1, C6.1, C7.1, C8.1, C9.1, C10.1, C11.1, C12.1, C13.1, JP1.2, LOGICCAP.+, SR1.10 (SCL), SR1.16 (VCC), SR2.10 (SCL), SR2.16 (VCC), SR3.10 (SCL), SR3.16 (VCC), SR4.10 (SCL), SR4.16 (VCC), SR5.10 (SCL), SR5.16 (VCC), SR6.10 (SCL), SR6.16 (VCC), SR7.10 (SCL), SR7.16 (VCC), SR8.10 (SCL), SR8.16 (VCC), SR9.10 (SCL), SR9.16 (VCC), SR10.10 (SCL), SR10.16 (VCC), SR11.10 (SCL), SR11.16 (VCC), SR12.10 (SCL), SR12.16 (VCC), SR13.10 (SCL), SR13.16 (VCC)

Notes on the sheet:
For all PN MOSFETs (Rows and Cols) -------------------------------------------- Lower numbered (name) resistor goes on lower section of ea group of PN MOSFETs. P is top MOS, N is bottom MOS.
logic vcc

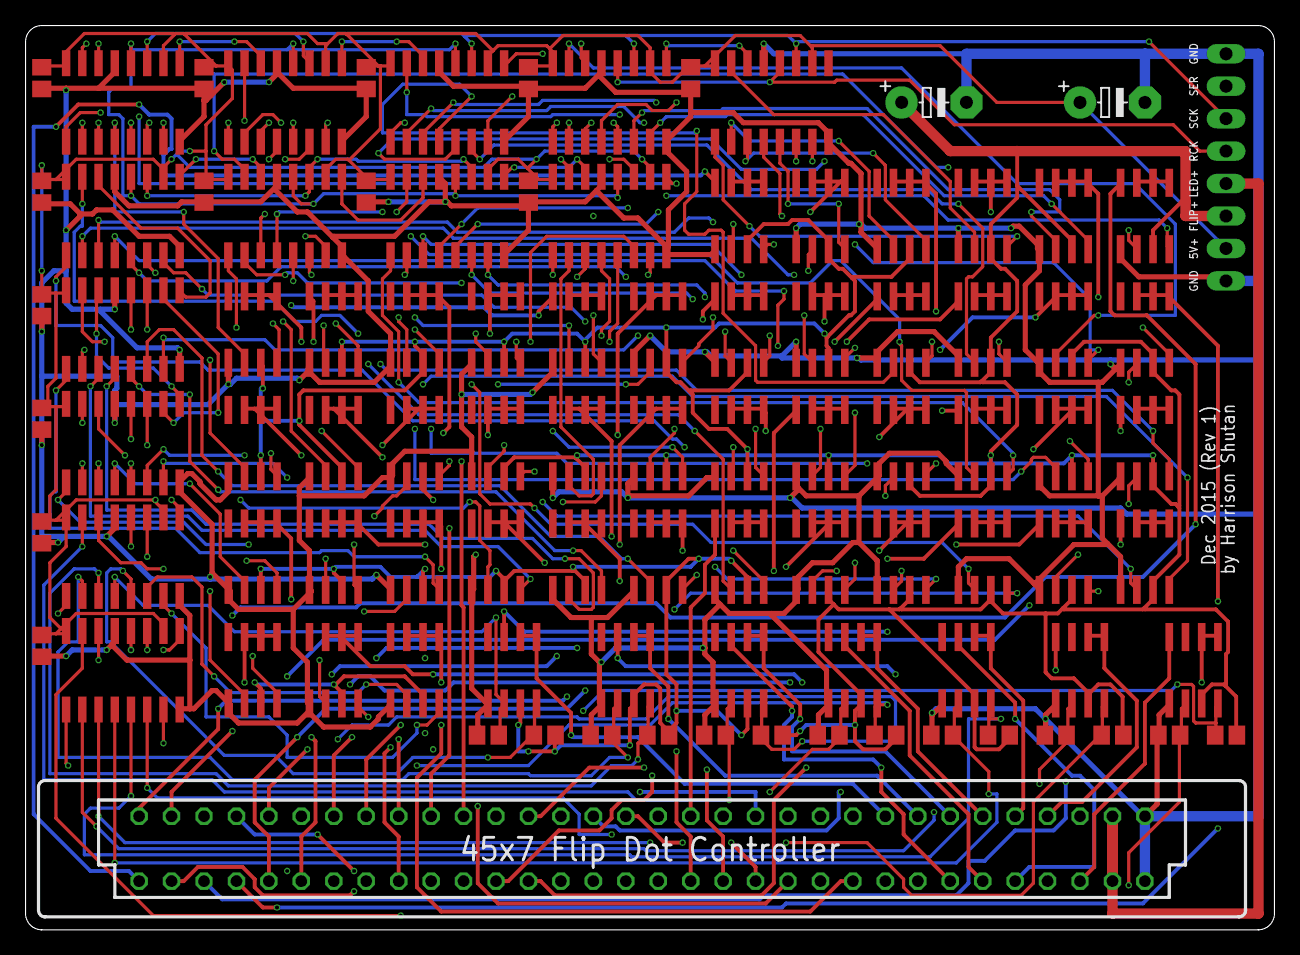
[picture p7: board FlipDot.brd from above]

Board: 4 copper layers, 97.8 x 70.8 mm, 96 parts (0 on the bottom side), 182 nets.

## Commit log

2015-12-27 Initial Seed Commit. (Rev 1)
    This is the first hardware revision of my 45x7 flip dot controller
    board. This has been sent to fab and works with a Luminator MAX3000 45x7
    side sign single panel.
    [FlipDot.brd, FlipDot.sch]
2015-12-27 Add bill of materials needed to produce PCB
    [FlipDotBOM.csv]
